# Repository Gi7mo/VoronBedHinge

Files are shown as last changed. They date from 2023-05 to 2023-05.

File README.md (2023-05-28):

**Voron 2.4 Bed Hinge Mod**

Voron Bed Hinge Mod, as i'm too lazy flip my printer everytime i wan't to access the electronics.
Don't know what inverted electronics mod was i used in my 2.4, but as i used the mod of [LoganFraser](https://github.com/VoronDesign/VoronUsers/tree/master/printer_mods/LoganFraser/TridentInvertedElectronics) in my trident, i highly recommend that.
I tested this bed hinge mod only on a 300 spec Voron, if and how it fits other sizes, i can't tell.

**BOM**
|Part NO.  |Qty  |Ali|
|--|--|--|
| Gas Spring 100n | 2 | [Link](https://s.click.aliexpress.com/e/_DluMizP)|
| Brass Heatset Inserts - M3x5x4 | 6 | [Link](https://s.click.aliexpress.com/e/_DEYZcUl)|
| M5x16 BHCS ISO 7380-1 | 2 | [Link](https://s.click.aliexpress.com/e/_DBHI0Xx)|
| M5x10 BHCS ISO 7380-1 | 6 | [Link](https://s.click.aliexpress.com/e/_DnS0m6D)|
| M3x6 BHCS ISO 7380-1 | 4 | [Link](https://s.click.aliexpress.com/e/_Ddd8Uah)|
| M3x8 BHCS ISO 7380-1 | 6 | [Link](https://s.click.aliexpress.com/e/_Ddd8Uah)|
| M3x16 BHCS ISO 7380-1 | 4 | [Link](https://s.click.aliexpress.com/e/_DnN3TNT)|
| M3 Roll-in Nut | 8 | [Link](https://s.click.aliexpress.com/e/_DDP9fut)|
| M5 Roll-in Nut | 8 | [Link](https://s.click.aliexpress.com/e/_DkqEN7P)|
| 20x20 profile hinges | 2 | [Link](IMAGES/joint_connector.png)|

for all bed connections i used some ponenix contact MSTBT 2,5/15-ST-5,08 connectors
[order number 1781111](https://www.buerklin.com/de/p/phoenix-contact/steckverbindersysteme/1781111/63P6292/) and [order number 1788664](https://www.buerklin.com/de/p/phoenix-contact/steckverbindersysteme/1788664/63P7120/)

**Pre-Assembly**
- order all the hardware
    - for the joint connector i recommend a connector that can be clamped, so it can't wobble
- print all the parts with voron standard settings
    - they are all oriented in the proper way
    - you don't need any supports, but proper cooling
    - use voron standard settings
    - use abs, ore more heat resistant material
        - others WILL melt and bent
- Order the custom [Deck Panel](DXF/deck_panel_300_lifted.dxf) at e.g. [Kuststoffplattenonline](https://kunststoffplattenonline.de/product/alupanel-alu-verbundplatten-schwarz-3-mm/) (they offer the service for some more european countries, just look at their footer)
    - i choosed that service, as i can upload the dxf for production

**Assembly**
- insert the heat inserts into the gasspring holders
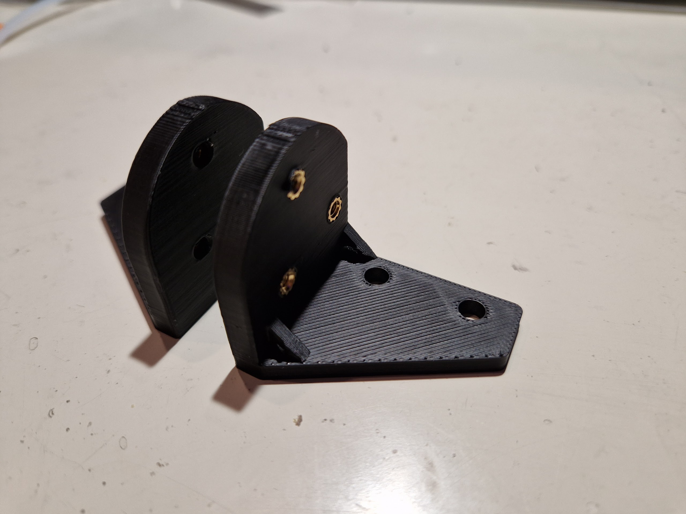
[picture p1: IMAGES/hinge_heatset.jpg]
heatset
- 
- bolt on the round metal gasspring holder with the M3x8 BHCS screws
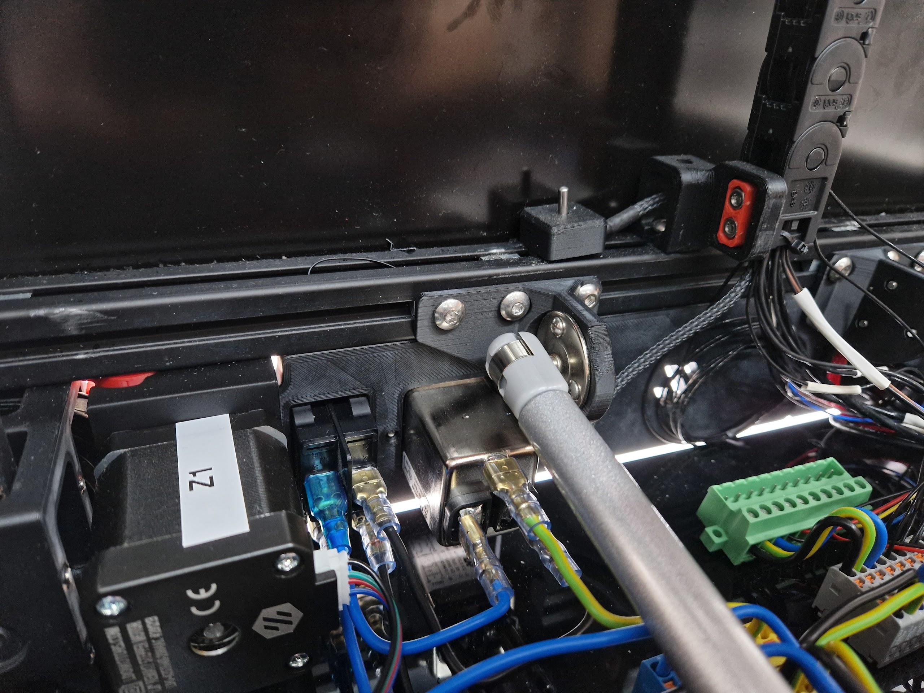
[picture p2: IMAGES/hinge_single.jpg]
hinge_single
- 
- bolt them to the rear of the frame with the M5x10 BHCS
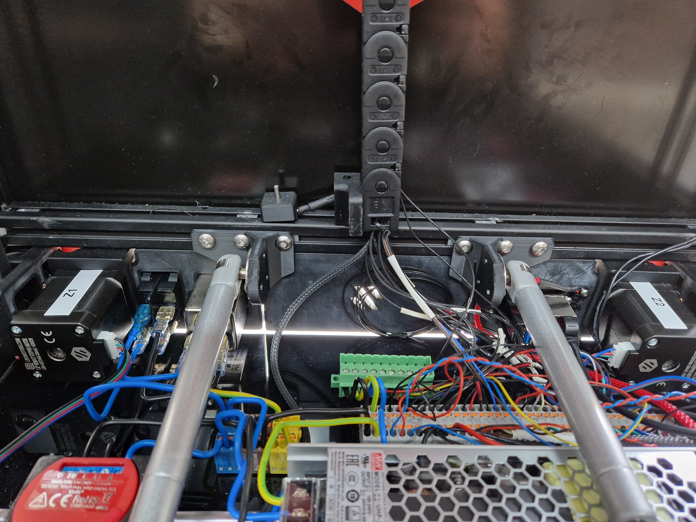
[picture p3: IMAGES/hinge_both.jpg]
hinge_both
- 
- disassemble your bottom deck plate
- bolt on the printbed stabilitzer, more to the rear, mind the space for e.g. a nevermore
- bolt on the printbed handle
- bolt on the joint connectors
- flip the howl deck assembly and assemble the gasspring holders (the hinge balls should look totwards the outside of the bed) <sub>°</sub>-| |-<sub>°</sub>
    - don't fully tighten the screws for the deck gasspring holders
- add the deck spacers
- bolt on the new bottom deck plate with the deck screw plates and the M3x16 BHCS screws
    - don't tighten them too much, as the screw plates will flex
- bolt the bed assembly with the joint connectors into the printer
- use some zip ties, cord, wire, whatever you have to keep the bed in an upright position
- insert the gasprings into their holders
    - you might have to open the retainers a bit with a screwdriver
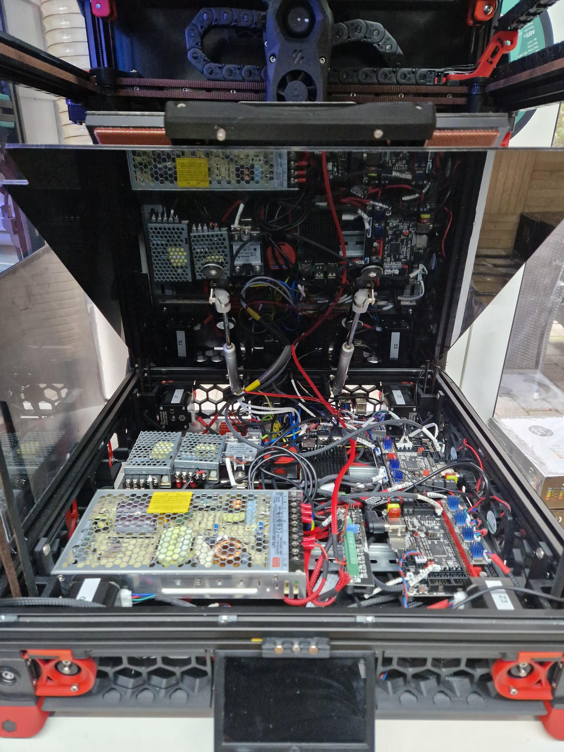
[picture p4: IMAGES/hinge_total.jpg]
hinge_total
- 
- align the gassprings, so they will push straight
- now use a ballhead screwdriver to fully tighten the screws of the deck gasspring holders
- remove the bed retainer (zipties, cord, whatever) and slowly close the bed
- insert some M5x16 BHCS into the bed handle
- you are done

## Notes
- You can contact me via Discord "Gi7mo!#4618"
- This readme file contains Amazon Associate, Aliexpress affiliate, PCBWay affiliate links. I make a comission on qualifying purchases.
- This project does not come with any warranty, if you choose to build/use one, you are doing this at your own risk!
- special thanks to [xbst](https://github.com/xbst/VoronUsers/tree/master/printer_mods/xbst_/Bed_Hinge) whose mod inspired me for mine
- special thanks to homewerken, who originally designed the bed handle and brace

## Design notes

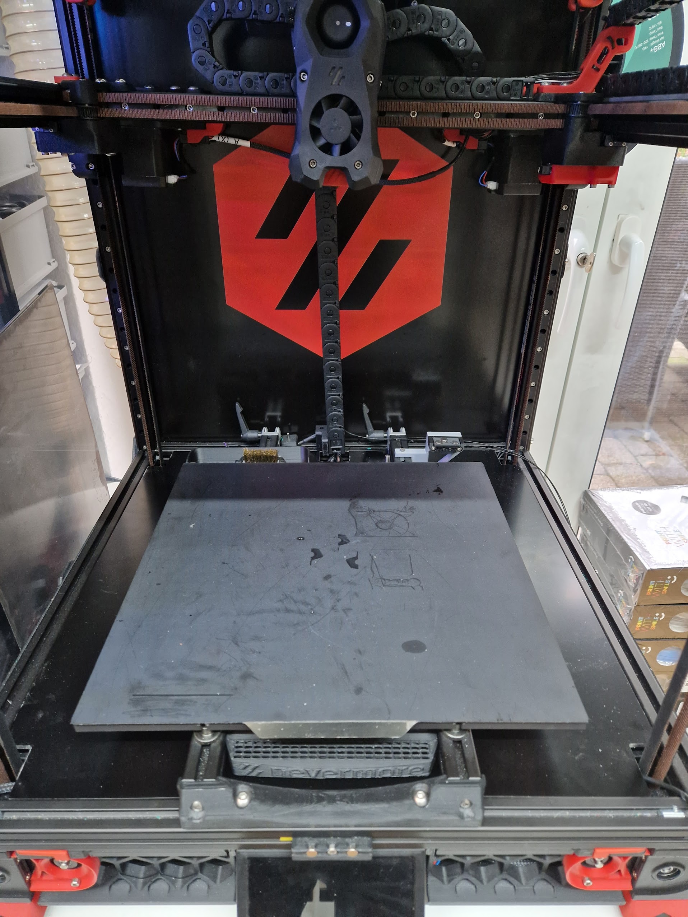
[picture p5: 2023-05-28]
IMAGES/hinge_topview.jpg

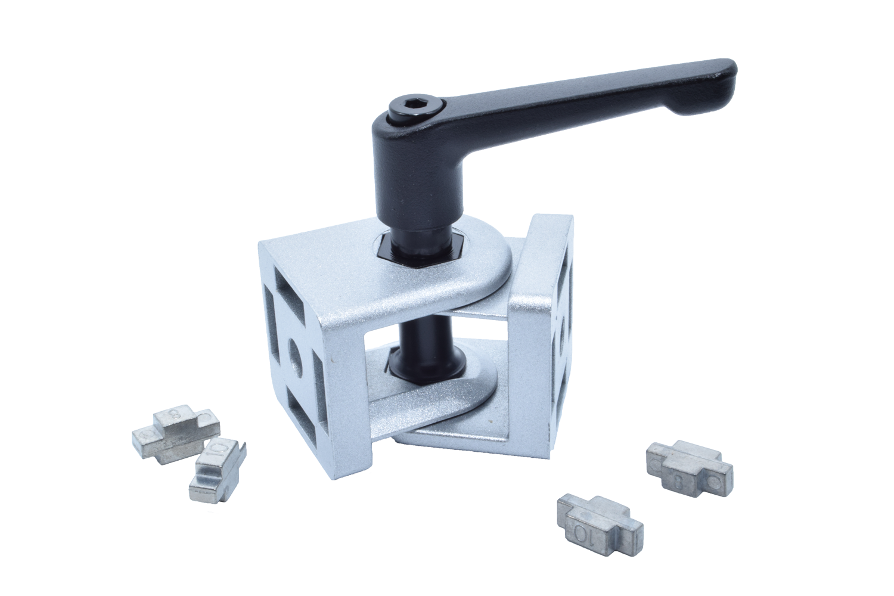
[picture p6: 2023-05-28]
IMAGES/joint_connector.png

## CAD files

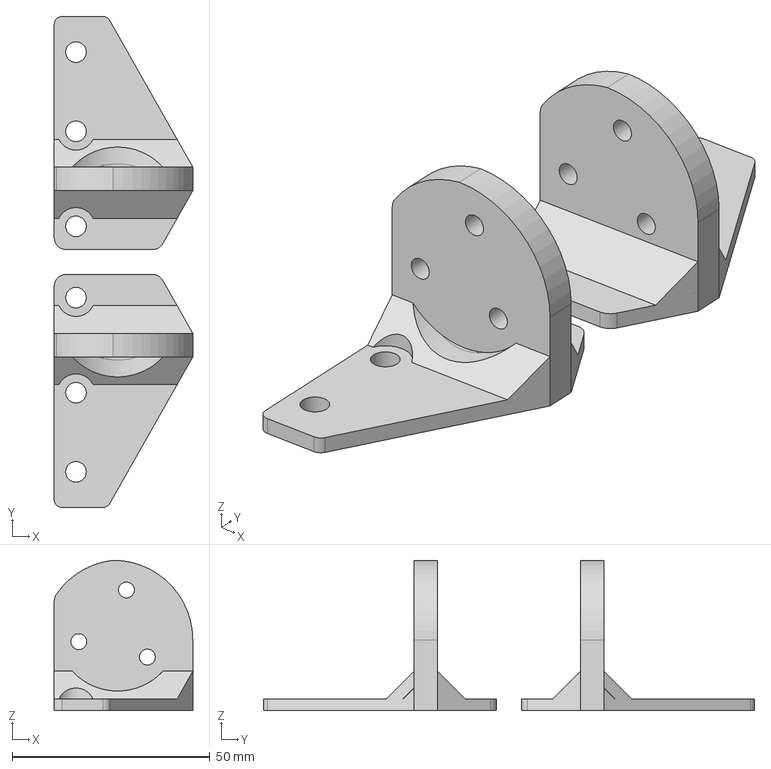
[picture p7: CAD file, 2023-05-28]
CAD/gasspring holder.step
35.0 x 124.0 x 38.0 mm

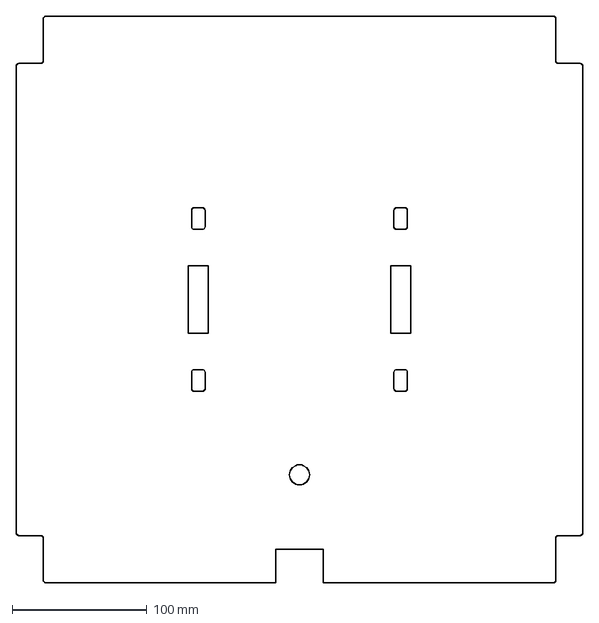
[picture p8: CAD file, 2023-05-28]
DXF/deck_panel_300_lifted.dxf
420.0 x 420.0 mm

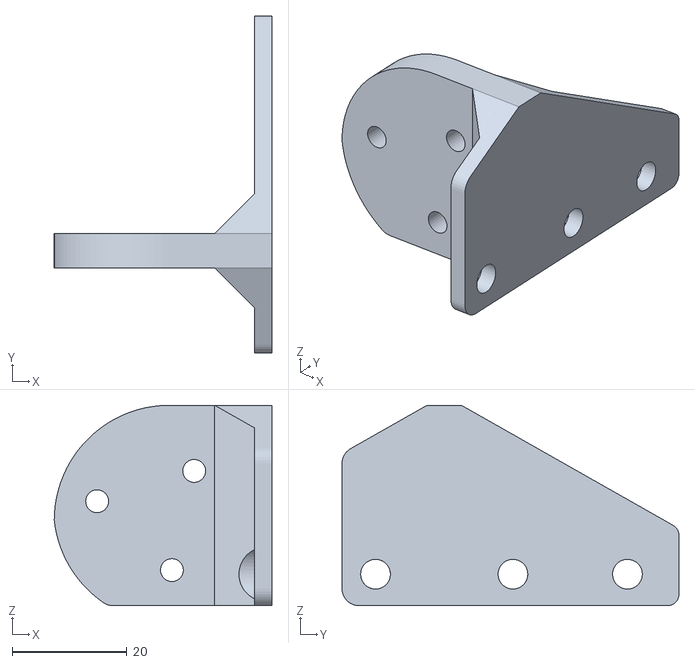
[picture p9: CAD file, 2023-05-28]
STL/gasspring_holder_left_x1.stl
38.0 x 58.9 x 35.0

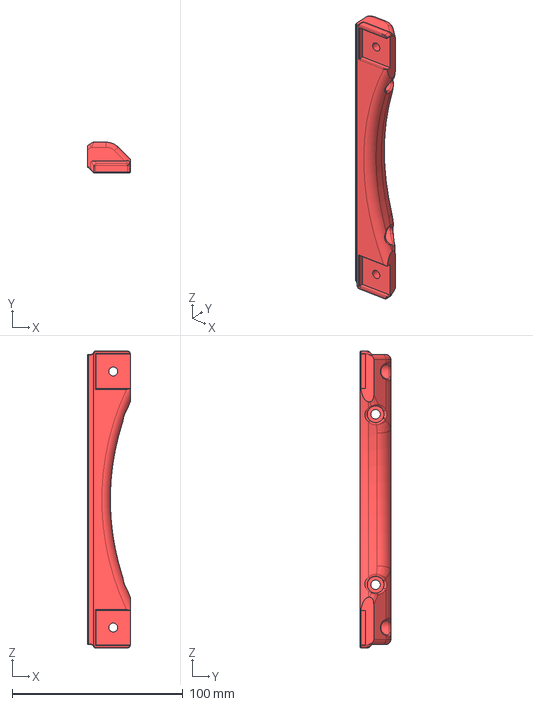
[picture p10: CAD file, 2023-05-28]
CAD/printbed handle.step
25.0 x 18.0 x 174.2 mm

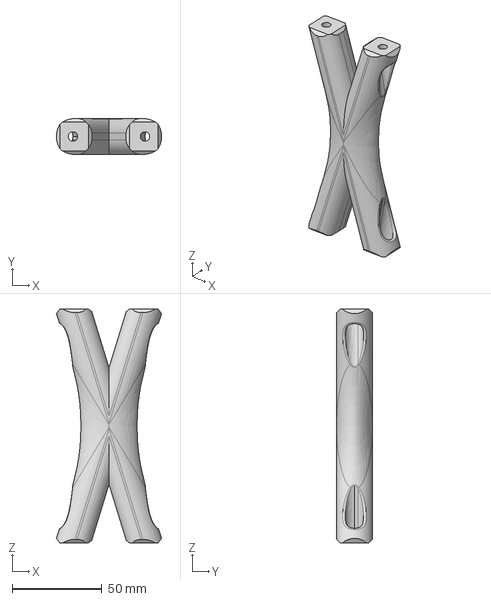
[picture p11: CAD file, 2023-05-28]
CAD/printbed stabilizer.step
58.4 x 20.0 x 130.0 mm

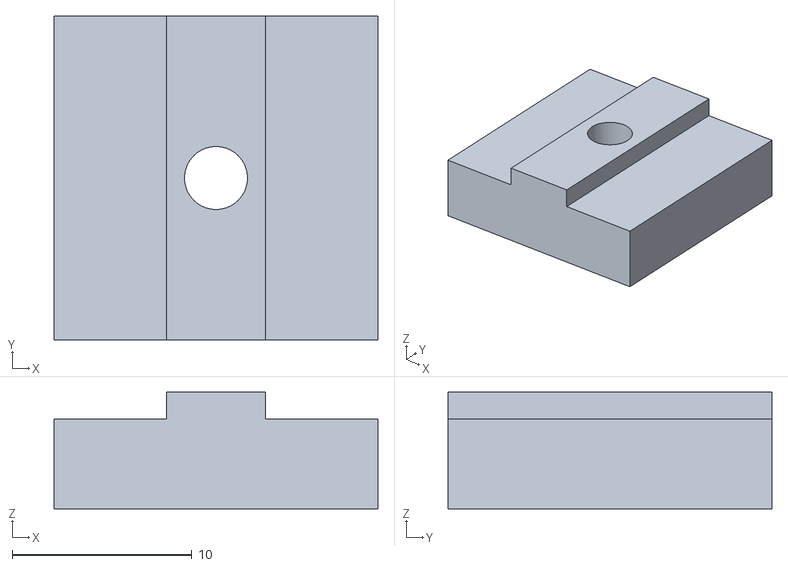
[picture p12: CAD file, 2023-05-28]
STL/deck_spacer_x4.stl
18.0 x 18.0 x 6.50

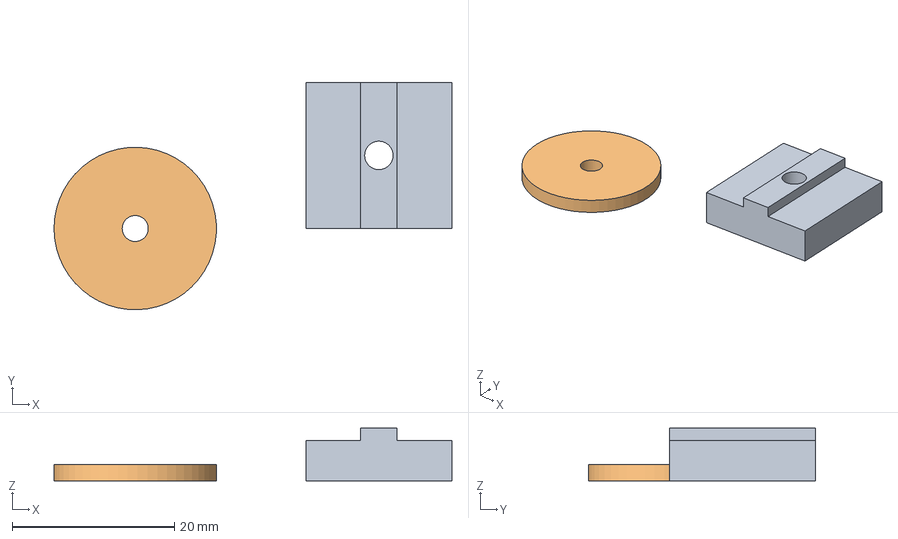
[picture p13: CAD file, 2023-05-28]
CAD/bottom deck fasteners.step
49.0 x 28.0 x 6.50 mm

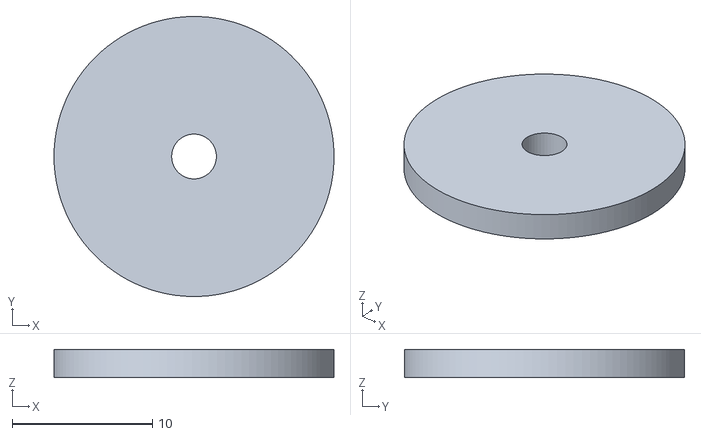
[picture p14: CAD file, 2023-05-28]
STL/deck_screw_plate_x4.stl
20.0 x 20.0 x 2.00

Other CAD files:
STL/gasspring_holder_right_x1.stl
STL/printbed_handle.stl
STL/printbed_stabilizer.stl

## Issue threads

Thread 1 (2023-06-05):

Print orientation of Gas Spring Holder L/R

bdistin, 2023-06-05:
I printed without changing the orientation but Found the mounting was weak along layer lines. It would be better orientated with the flat side down (the side that goes against the extrusion) like how one of your photos shows instead.

Gi7mo, 2023-06-05:
thanks for your feedback
printing it the other way around was my first intention too, but it broke after a few days
it broke at 90° link from extrusion to gaspring holder

oriented like in this repo, it holds up for a few month for me

Closed 2023-09-03.
